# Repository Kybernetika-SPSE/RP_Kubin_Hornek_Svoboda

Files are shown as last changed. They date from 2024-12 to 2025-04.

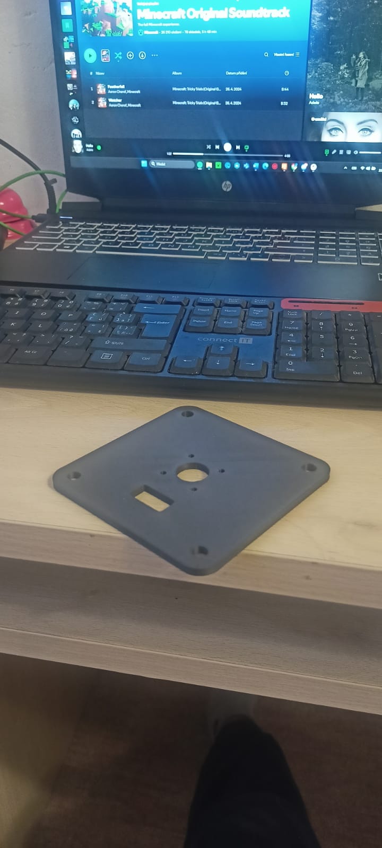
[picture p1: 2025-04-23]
Dokumentace/Progress/Hornek/Dilci_vypracovani/Fotky/m2 podložka.jpg

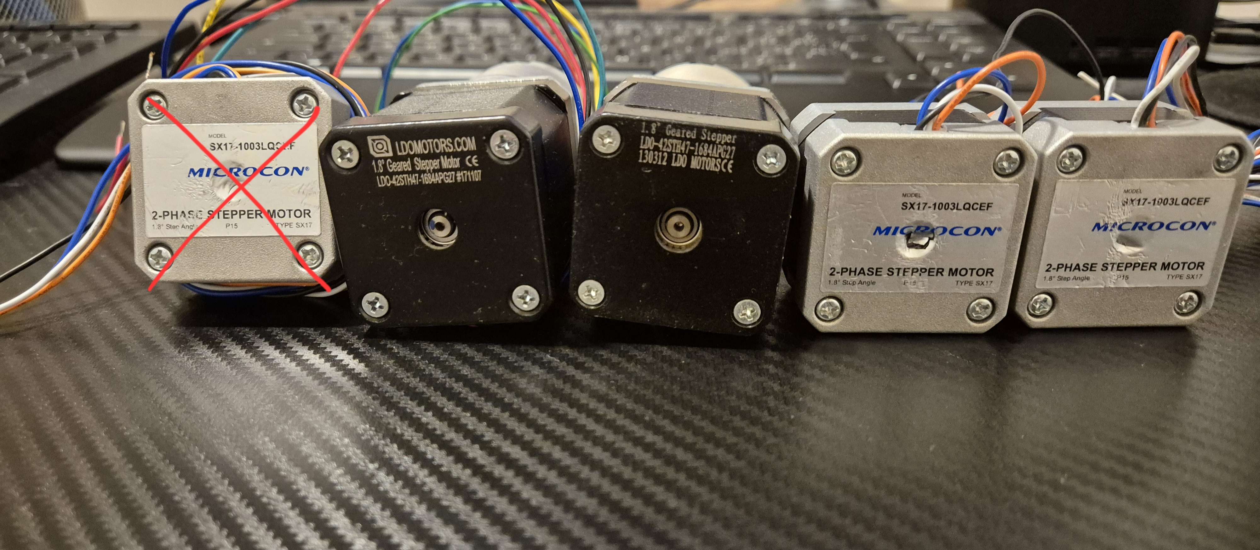
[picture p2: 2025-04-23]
Dokumentace/Progress/Hornek/Dilci_vypracovani/Fotky/20250423_202752.jpg

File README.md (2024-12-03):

Model průmyslového šestiosého robota

Baví nás průmyslové technologie a robotika. Chceme sestavit model průmyslového kolaborativního robota, udělat k němu pendant a provést oživení.
Příští rok bychom toto rádi rozvinuli i do maturitní práce. Očekáváme, že získáme více praxe a více porozumění v tomto oboru a do budoucna nám budou velmi přínosné, ať už v práci, nebo na vysoké škole.
A hlavně... jsme borci

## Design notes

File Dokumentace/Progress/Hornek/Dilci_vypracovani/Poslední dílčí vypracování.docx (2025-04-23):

# Poslední dílčí vypracování

V složce robot jsou veškeré modely, které jsou ve finálním stavu a už se nebudou měnit, takže robot má 4 funkční osy, na dalších dvou se pracuje a brzo budou. Ve složce fotky jsou fotky částí robota, které jsou úspěšně vytisklé. Máme tam dále fotku všech motorů a jednoho motoru na kterém je spojka, kterou budu využívat k uchycení mezi 3. a 4. osou, a mezi 4. a 5. osou. Odkaz na ní: https://www.laskakit.cz/pruzna-spojka-hlinikova-sviraci-5x8mm/

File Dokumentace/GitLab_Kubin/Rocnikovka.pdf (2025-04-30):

## Vyšší odborná škola

## a Střední průmyslová škola elektrotechnická

## Plzeň, Koterovská 85

## ROCNˇ ÍKOVA PR ´ ACE ´

### Téma:

# Model průmyslového šestiosého robota

Autor práce: | Tomáš Kubín
Třída: | 3.L

## Vedoucí práce: Jiří Svihla ˇ

Dne: | 30. 4. 2025

## Hodnocení:

V Plzni dne: 29. 11. 2024 | Mgr. Jan Syřínek, v.r. Zástupce ŘŠ, zástupce statutárního orgánu Vedoucí organizace VOŠ, SŠ, DM

## Vyšší odborná škola a Střední průmyslová škola elektrotechnická Plzeň, Koterovská 85

## Z A D Á N Í R O Č N Í K O V É P R Á C E

Školní rok | 2024/2025
Studijní obor | 78 – 42 – M/01 Technické lyceum
Jméno a příjmení | Tomáš Kubín
Třída | 3.L
Předmět | Kybernetika
Hodnoceno v předmětu | Kybernetika
Téma | Model průmyslového šestiosého robota
Obsah práce | Tvorba řízení (softwarová část) pro model průmyslového kolaborativního robota. • Výběr komponent (20. 12. 2024) • Prototyp řízení (24. 1. 2025) • Finalizace zařízení a napojení na síť (28. 2. 2025) • Tvorba dokumentace (28. 3. 2025)
Zadávající učitel Příjmení, jméno | Švihla Jiří
Termín odevzdání | 30. dubna 2025

## Anotace a poděkování

Má ročníková práce se zabývá tvorbou řízení pro model kolaborativního průmyslového

robota. Cílem bylo vytvořit ne příliš komplexní, avšak efektivní systém jako celek za

pomoci běžně dostupných komponent. Na jiných částech robota pracovali Daniel Hornek

a Matěj Svoboda.

Chtěl bych poděkovat firmě Würth Elektronik za poskytnutí pasivních a elektromechanických součástek do desky plošných spojů zdarma, vedoucímu práce Jiřímu Svihlovi za ˇ

podporu při zpracování, krokové motory a vyfrézování.

Prohlašuji, že jsem tuto práci vypracoval samostatně a použil literárních pramenů a informací,

které cituji a uvádím v seznamu použité literatury a zdrojů informací.

Prohlašuji, že jsem nástroje UI využil v souladu s principy akademické integrity a že na

využití těchto nástrojů v práci vhodným způsobem odkazuji.

Nesouhlasím s využitím mé práce učiteli VOS a SP ˇ | SE Plzeň k výuce. ˇ
V Plzni dne 30. 4. 2025 | Podpis: |

## Obsah

Uvod ´ | 6
1 Cíle | 7
2 Komponenty | 9
3 Návrhový software | 14
4 Komunikace | 18

5 Kód na Raspberry Pi Pico | 21
6 Kód na Raspberry Pi 4 | 24
Závěr | 26
Přílohy | I

## Uvod ´

V současné době, kdy se rozvíjí koncept průmyslu 4.0, je trendem výrobní procesy co

nejvíce automatizovat, a proto se hojně využívá robotů. Kolaborativní roboti jsou schopni

spolupracovat s člověkem za absence většiny bezpečnostních prvků nutných u tzv. dospělých

robotů. To mě dovedlo k myšlence zkusit si jednoho postavit, protože v běžném provozu

si s nimi člověk hrát nemůže a nejedná se ani o běžně přístupné ”hračky.”

Podílení na stavbě jednoho je přínosnou zkušeností nejen z kreativního a programátorského

hlediska, ale i z oblasti spolupráce a organizace projektu více lidí.

6

## 1 Cíle

Mým cílem bylo vyvinout řízení pro model průmyslového robota. Věnoval jsem jak soft-

warové části řízení, tak i té nezbytné hardwarové.

### 1.1 Softwarové cíle

Software jsem nechtěl od samého začátku dělat zbytečně komplikovaný, funkčnosti a od-

laděnosti jsem dával přednost. Programoval jsem s myšlenkou variabilnějšího použití ro-

bota, mezi které řadím například modularitu, jiné počty a typy motorů. Tedy jsem neo-

pomenul rozšíření projektu v budoucnu do takové míry, kdy bude v podstatě jen stačit

změnit konfigurační soubor.

Cíle bych shrnul následovně:

1. Základní ovládání motorů
2. Komunikace
3. Optimalizace a přidání ”nice to have”funkcí

### 1.2 Hardwarové cíle

Již od začátku jsem chtěl všechno umístit do rozvaděče. Tomu jsem uzpůsobil výběr komponent. To bylo primárním důvodem pro návrh vlastní desky plošných spojů (DPS). Mi-

nimalizace byla pro mě nesmírně důležitá, chtěl jsem alespoň vnější konstrukci rozvaděče

být schopen vytisknout na klasické 3D tiskárně.

Shrnutí cílů:

7

1. Výběr komponent
2. Návrh DPS
3. Tvorba rozvaděče

8

## 2 Komponenty

### 2.1 Raspberry Pi Pico 2

Aby bylo zajištěno rychlé ovládání motorů, byl zvolen mikrokontrolér Raspberry Pi Pico 2.

Ten slouží výhradně k obsluze vstupů a výstupů. Přistoupil jsem k variantě bez bezdrátových

možností, všechna komunikace je totiž řešena spolehlivě drátovou cestou.

Raspberry Pico 2 je vybaveno procesorem RP2350A vlastní výroby - dvě jádra M33 Cortex a frekvence 150 MHz. Na desce je 4 MB flash pamět’, která postačí i na náročnější

projekty. Pamět’ RAM je v porovnání s předchozí generací téměř dvojnásobná, tzn. 520

KB. (Raspberry Pi Ltd 2025b)

Velkou výhodou této desky je její popularita ve světě. To se odráží na její dostupnosti a v komunitě není obtížné najít pomoc při případných obtížích (hardwarových i softwa-

rových).

Já osobně ji programuji v MicroPythonu, lze však využít i jazyk C a Arduino IDE.

Celkem má 40 pinů, dvacet na každé straně. Rozmístění pinů včetně popisků mnou

použitých je na výňatku z přílohy I, na obrázku 2.1. Všech 28 dostupných GPIO pinů je

využito.

UART má dva kanály, z nichž jsem použil ten druhý a má pevně dané piny 6 a 7 na levé

straně.

Napájení je zajištěno přes VSYS. Mezi zdrojem a VSYS je ještě zapojena schottkyho

dioda, aby nedocházelo ke zpětnému napájení.

9

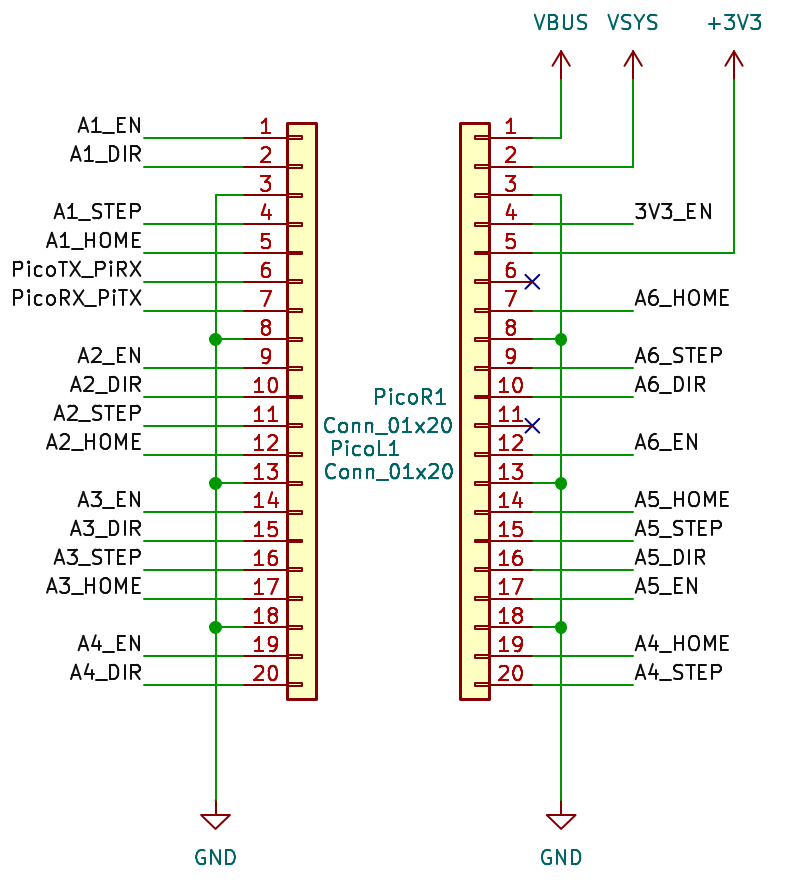
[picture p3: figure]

Obrázek 2.1: Zapojení pinů na Picu [Zdroj: vlastní]

10

### 2.2 Raspberry Pi 4

Raspberry Pi 4 není mikrokontrolérem, nýbrž se jedná o relativně výkonný a univerzální jednodeskový počítač. V mém projektu zajišt’uje komunikaci s mikrokontrolérem a pen-

dantem.

Mezi jeho hlavní přednosti se v mém případě řadí možnost instalace plnohodnotného

operačního systému, což je ideální pro budoucí rozšíření, jako je například hostování

vlastní databáze, webového serveru či jiných náročnějších aplikací.

Stejně jako Raspberry Pi Pico je široce rozšířené a dostává se podpory rozsáhlé komunity.

Má taktéž 40 pinů, v nichž se od Raspberry Pi Pico velmi liší. Za mě je významnou

výhodou více kanálů pro UART. Lze tedy k němu připojit moje Pico, pendant a ještě zůstane velká rezerva. (Raspberry Pi Ltd 2025a)

### 2.3 Drivery pro krokové motory DRV 8825

Pro řízení krokových motorů je nutné použití driveru. Po konzultaci jsem se rozhodl pro DRV8825 od Texas Instruments. Je určen pro bipolární krokové motory (motor má dvě

cívky, tedy z něj vedou 4 dráty, které musíme zapojit) použité v projektu.

Nastavení proudového limitu je možné pomocí malého potenciometru, což chrání motor.

Vyšší proudy vyžadují chlazení, alespoň pasivní.

Neméně důležitou vlastností je mikrokrokování (úprava počtu kroků na celou otáčku), to

lze nastavit v rozsahu od 1 až po 1/32 (zmenšit jde jen po polovinách).

Rozmístění pinů je na obrázku 2.3 (Bakker 2025).

Piny M0, M1, M2 slouží k nastavení mikrokrokování, návod je na DPS.

K pinům A1, A2, B1 a B2 se připojuje vinutí motoru.

Pro funkci je nutné přivést 3 V na piny RESET a SLEEP.

11

Pin ENABLE je vždy zapojen na výstup, aby se motory daly jednoduše vypnout.

Na VMOT je přivedeno 12 V jako napájení motorů. Driver umí i motory s větším vstupním

napětím.

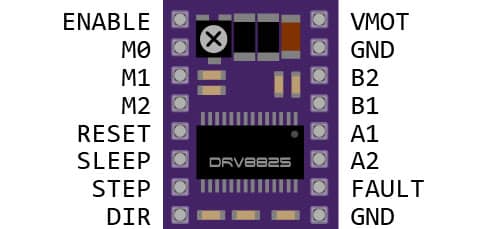
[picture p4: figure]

Obrázek 2.2: Rozmíst’ěný pinů na driveru [Zdroj: makerguides.com]

### 2.4 Rozvaděč

Rozvaděč jsem vymyslel do jisté míry modulární. Spodní a horní část jsem navrhl tak,

aby se dala bez problému vytisknout na 3D tiskárně. Obě části mají výřezy na zasouvací

stěny.

Hrany stěn a složité útvary, které by nešly vytvořit jiným způsobem, jsou vyfrézovány do dřevěné desky o tloušt’ce 3 mm. Díry pro úchyty DPS, Raspberry Pi 4, zdroje jsou

dodatečně vyvrtány vrtačkou a tudíž nebudou zahrnuty ve výkresech. Zdrojové soubory pro rozvaděč jsou v GitHub repozitáři (Kubín 2025).

12

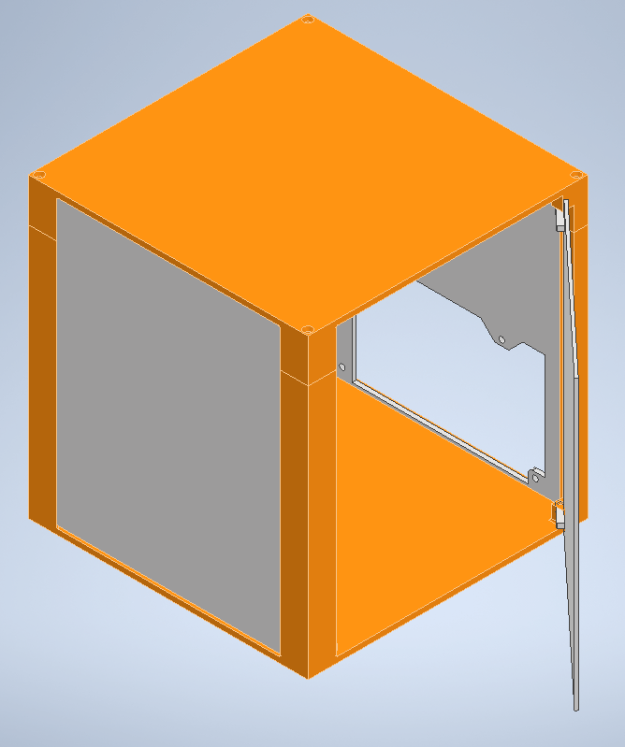
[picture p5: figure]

Obrázek 2.3: Rozvaděč ve 3D návrhovém softwaru [Zdroj: vlastní]

13

## 3 Návrhový software

Po výběru komponent bylo důležité se rozhodnout, v jakých jazycích a nástrojích budu

tvořit.

### 3.1 Visual Studio Code (VS Code)

Veškerý kód jsem vyvíjel v jazyce Python (resp. MicroPython). Rozhodl jsem se pro

populární IDE Visual Studio Code vyvíjené společností Microsoft. Zkoušel jsem předtím

často v komunitě doporučovaný Thonny, ale ten mi připadal jako příliš jednoduchý a omezující

program.

Mezi nejdůležitější přednosti VS Code řadím hlavně ty zvyšující uživatelský komfort. VS

Code má pro mě nesmírně důležité zkratky ”Ctrl+Tab”a skvěle fungující ”Tab”, které

bohužel stále v dnešní době moc programů neumí. Nabízí možnost členit kód do regionů,

které lze skrýt, což je výrazná výhoda pro lepší orientaci.

Na obrázku 3.1 je prostředí s otevřeným kódem. Na obrázku 3.2 je detail pravého horního

rohu, kde se v přehledu ukazují názvy regionů, případně se zvýrazní stejné proměnné, když

na nějaké stojíte.

Do VS Code jde doinstalovat spoustu rozšíření, kterých jsem samozřejmě využíval.

Primárně tyto:

1. Micro Pico (Random Nerd Tutorials 2025)

Tento doplněk umožňuje programovat Raspberry Pi Pico. Umožňuje i ukládání

a mazání souborů z Pica. Slouží také ke spouštění kódů na Picu bez nutnosti je

mít na něm uložené a čtení dat z konzole.

2. Remote Explorer

14

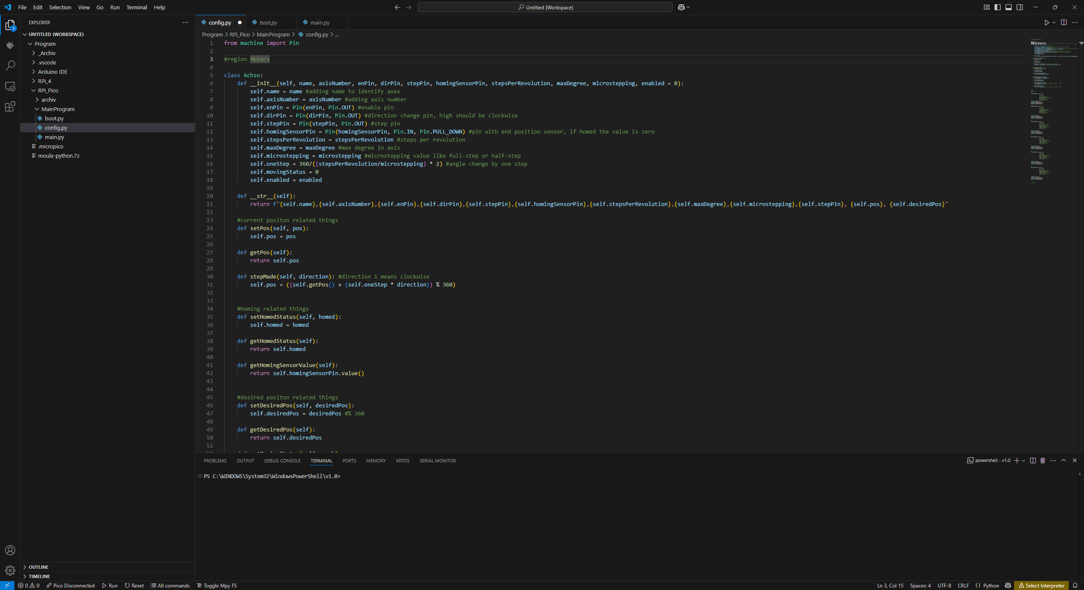
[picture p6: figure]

Obrázek 3.1: VS Code s otevřeným python skriptem [Zdroj: vlastní]

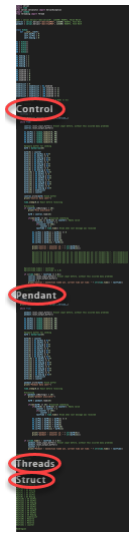
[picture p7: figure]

Obrázek 3.2: Detail pravého horního rohu z VS Code [Zdroj: vlastní]

15

Jedná se o doplněk, který se prostřednictvím SSH připojí na vzdálenou stanici,

my mu specifikujeme, kterou složku má vždy otevřít, tou procházíme a otevíráme

soubory s kódem, které po každé změně musíme uložit a přes terminál ve spodní

části obrazovky spustit.

### 3.2 KiCad

KiCad je volně dostupným programem pro návrh desek plošných spojů (DPS). Já jakožto

začátečník oceňuji jeho jednoduchost a hned jsem se s ním sžil.

Jedná se v podstatě o balík různých nástrojů, do kterých je i členěn viz. obrázek 3.4,

a ty pospolu fungují jako celek. Mezi mnou nejvíce využívané patří schematický, PCB

a footprint editor.

KiCad umožňuje instalaci doplňků, které mohou zjednodušit export potřebných souborů pro výrobu specializovanou firmou. Můj projekt je na GitHubu (Kubín 2025).

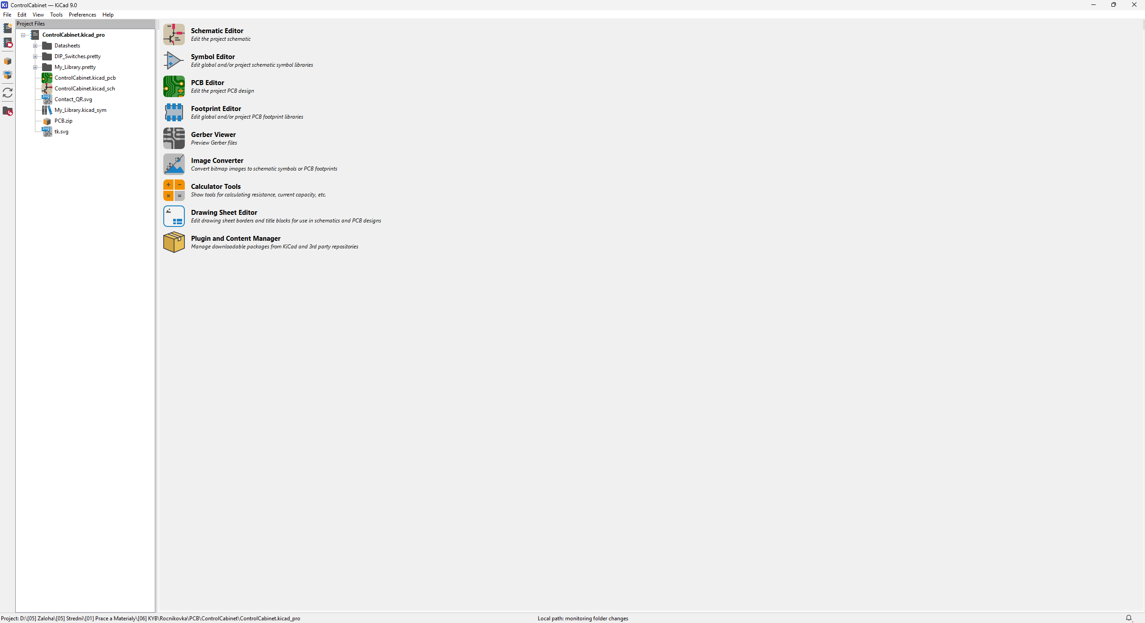
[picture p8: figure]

Obrázek 3.3: Pohled na základní prostředí KiCadu s otevřeným projektem [Zdroj: vlastní]

16

### 3.3 Autodesk Inventor

3D modely pro rozvaděč jsem vytvářel v profesionálním programu Autodesk Inventor.

Jedná se o program, který využívá naše škola ve výuce. Proto mi nepřišel cizí a odpadlo

učení se něčeho nového.

Kromě tvorby 3D modelů umožňuje i vytváření sestav a výkresů. Výkresy se nechají

všelijak upravovat, vlastní razítko, rámečky atd.

Nativně podporuje export modelů do .stl či .stp souborů pro tisk.

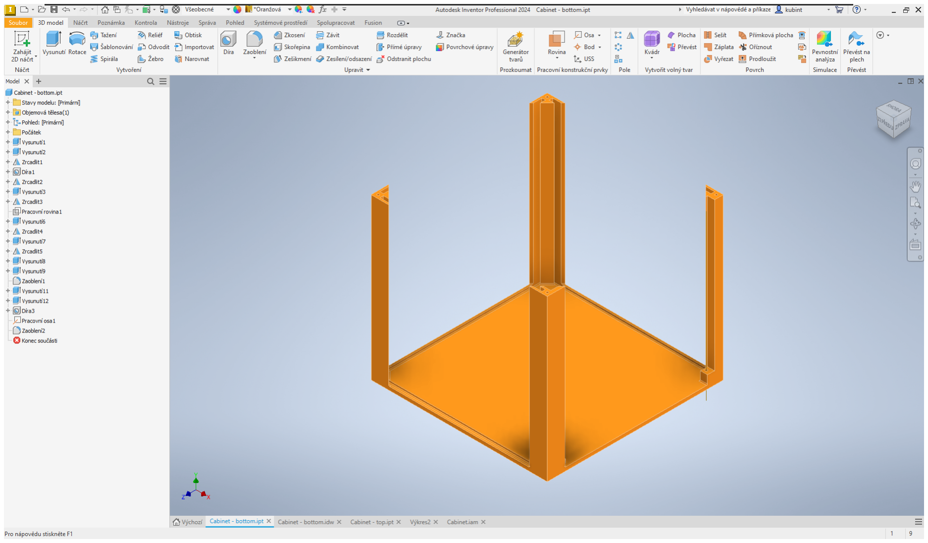
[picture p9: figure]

Obrázek 3.4: Pohled na základní prostředí Inventoru s otevřeným projektem [Zdroj: vlastní]

17

## 4 Komunikace

Komunikace mezi oběma Raspberry a pendantem je dělána přes UART. Jedná se o jedno-

duchý asynchronní komunikační protokol, kterému stačí jen dva vodiče. Po jednom jedna strana odesílá data (Tx) a druhá přijímá (Rx), u druhého drátu je směr komunikace

opačný.

UART dovoluje nastavit přenosovou rychlost (baudrate), jinými slovy počet bitů za

sekundu (bps). Já osobně jsem se rozhodl pro 115 200 bps, jedná se o kompromis mezi

rychlostí a spolehlivostí (ani na jedno si nemohu stěžovat)

V pythonu je jeho použití v kódu velmi jednoduché, netřeba instalovat dodatečné knihovny.

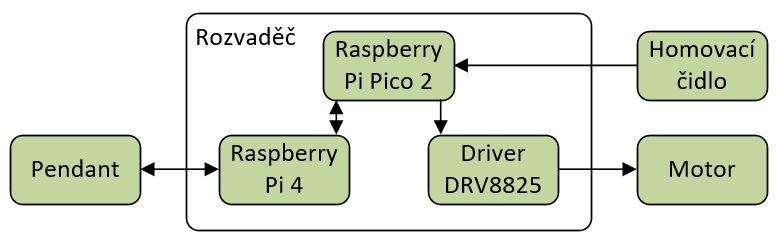
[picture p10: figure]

Obrázek 4.1: Komunikační diagram [Zdroj: vlastní]

### 4.1 Struktura dat

V rámci přehlednosti a rozumné kontroly nad posílanými daty jsem se rozhodl posílat

si vždy stejně dlouhé pole bajtů. Jeho struktura je popsána v tabulce 4.1. Struktura je

všude stejná jak pro Raspberry Pi Pico 2 tak pro pendant, jen některé hodnoty mají jiný význam (jednou aktuální pozice a jindy zas požadovaná).

Rozhodl jsem se pro 24 bajtů, nejedná se sice pěkně o mocninu dvou, ale nechtěl jsem

dělat zbytečně velkou rezervu. Rezervu jsem přidal pro jednoduchost přidávání budoucích

dat, odpadá potom nějaké to psaní navíc na všech stranách, takhle stačí jen menší úprava.

18

Pořadí bytu | Jeho obsah
0 | counter
1 | 1. byte požadované pozice první osy
2 | 2. byte požadované pozice první osy
3 | homing k první ose
4 | 1. byte požadované pozice druhé osy
5 | 2. byte požadované pozice druhé osy
6 | homing k druhé ose
7 | 1. byte požadované pozice třetí osy
8 | 2. byte požadované pozice třetí osy
9 | homing k třetí ose
10 | 1. byte požadované pozice čtvrté osy
11 | 2. byte požadované pozice čtvrté osy
12 | homing k čtvrté ose
13 | 1. byte požadované pozice páté osy
14 | 2. byte požadované pozice páté osy
15 | homing k páté ose
16 | 1. byte požadované pozice šesté osy osy
17 | 2. byte požadované pozice šesté osy
18 | homing k šesté ose
19 | seznam povolených os
20-22 | rezerva
23 | counter

Tabulka 4.1: Struktura posílaných dat z Raspberry Pi 4

19

První a poslední bajt obsahují vždy stejný counter (proměnná, která se čítá s každým

odesláním), který slouží k detekci přijatých nových dat a zároveň kontrole konzistence

(všechna data přišla v pořádku).

Natočení osy může být od 0° do 360°, zatímco maximální hodnota jednoho bajtu může

být 255. Proto jsem musel úhel natočení pomocí bitových operací rozdělit do dvou bajtů.

Následuje bajt, ve kterém jsou věci k homingu. Zatím se jedná spíše o neefektivně využitý

bajt, protože se v něm posílá jen jestli je osa homovaná respektive jestli má povolení se

homovat. V plánu je ale budoucí rozšíření, kde počítám s více parametry, proto tam tedy

nechávám jednotlivé bajty.

V 19. bajtu každý bit až na poslední je přiřazen jedné ose. Hodnota bitu TRUE znamená,

že osa je povolena, zatímco FALSE znamená, že je zakázána.

V budoucnu je v plánu strukturu upravit na posílání i desetinných čísel v případě natočení

motorů.

20

## 5 Kód na Raspberry Pi Pico

Veškerý kód tvořený pro Raspberry Pi Pico 2 jsem na něj uložil ve třech souborech. A je dostupný na GitHub repozitáři (Kubín 2025)

### 5.1 boot.py

Vlastností firmwaru je, že se soubor boot.py, je-li k dispozici, spustí automaticky po připojení napájení. Já osobně v něm jenom zablikám s LED, at’ vím, že Pico právě naběhlo.

### 5.2 main.py

Po dokončení kódu z boot.py se automaticky spustí main.py. V mém případě se jedná tedy

o soubor, ve kterém je uložen hlavní kód.

### 5.2.1 Vlákna

Z důvodu rychlosti (stačil jen jeden motor a byl poznat rozdíl) jsem musel implementovat

multithreading. Vytvořil jsem dvě vlákna, to první se stará o komunikaci s Raspberry Pi

4 přes UART a to druhé řeší pohyb motorů. Vlákna spolu sdílejí proměnné.

Napřed je třeba import knihovny _thread. V kódu mám vytvořené ony dvě funkce

s cyklem while. Vlákna se startují velmi jednoduše ve dvou řádcích:

second_thread = _thread.start_new_thread(control_thread, ())

uart_thread()

21

### 5.3 config.py

Soubor config.py je tvořen v podstatě jako knihovna. Je importován na začátku souboru

main.py.

Je v něm napsána poměrně rozsáhlá třída, která obsahuje veškeré vlastnosti pro jednotlivé

motory na každé ose.

Třída se v Pythonu vytváří následovně:

class Achse:

To ale samo o sobě nestačí, dovnitř začneme psát různé funkce. Asi tou nejdůležitější je

__init__, její vstupními parametry jsou v mém případě:

self, name, axisNumber, enPin, dirPin, stepPin, homingSensorPin, stepsPerRe-

volution, maxDegree, microstepping, enabled = 0.

Self je povinný argument. Vstupní proměnné obsahující slovo Pin jsou přímo číslo pinu,

na který je daná věc zapojena. Ostatní vstupní hodnoty jsou vlastnosti specifické pro

každou osu.

Dále obsahuje 11 funkcí, které zahrnují mimo jiné i nastavení požadované pozice, čtení

aktuální pozice a veškeré věci týkající se homování.

Po deklaraci třídy je potřeba vytvořit si proměnné (pro každou osu jednu). Pro lepší práci

s osami jsem si napřed vytvořil pole, do kterého jsem vložil proměnnou od každé osy. Na

obrázku 5.2 je vidět deklarace pole a připojení první osy k němu.

22

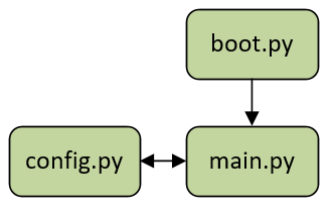
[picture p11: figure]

Obrázek 5.1: Diagram spouštění kódu na Pico 2 [Zdroj: vlastní]

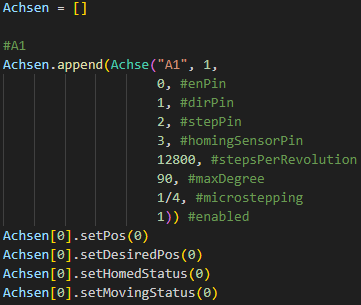
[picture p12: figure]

Obrázek 5.2: Připojení proměnné pro první osu do pole [Zdroj: vlastní]

23

## 6 Kód na Raspberry Pi 4

Situace se soubory je tentokrát mnohem jednodušší. Vše je psáno v souboru main.py.

Na rozdíl od Raspberry Pi Pico jsem musel ještě v pár jednoduchých krocích nastavit spouštění skriptu po startu. Kód je též na GitHubu (Kubín 2025).

### 6.1 Autostart skriptu

Postup pro nastavení automatického spouštění skriptu:

1. Spustíme terminál (lze i vzdáleně pomocí ssh, já preferuji program KiTTY)
2. Spustíme program crontab s parametrem e

crontab -e

3. Jsme dotázáni, v jakém editoru chceme editovat, volba je čistě na Vás
4. Pro spuštění kódu hned po startu přidáme do souboru

@reboot python3 /home/Code/main.py

5. Soubor uložíme a můžeme restartovat pro ověření funkčnosti. (Brown 2025)

### 6.2 Vlákna

Kód je i zde rozdělen do dvou vláken, jen pomocí knihovny threading. Implementace je

potom též poměrně jednoduchá a ve dvou řádcích:

Thread(target = comm_Control).start()

Thread(target = comm_Pendant).start()

24

Vlákna sdílejí některé proměnné. Jedná se jen o proměnné třídy s osami.

Spuštěné funkce si jsou velmi podobné, liší se jen drobnostmi. Já tedy vysvětlím jen

princip funkčnosti. Zakládal jsem si na tom, že zařízení jako celek bude ve stylu plug

and play, člověk se nebude muset o nic starat a po zapnutí napájení se komunikace sama

naváže.

Jsou použity dvě hlavní proměnné pro správu counter a lastTime, kdy nutnost counteru

již byla vysvětlena a proměnná lastTime, ukládající čas poslední komunikace, je nezbytně nutná pro detekci výpadku spojení (timeout).

Po naplnění send bufferu se buffer odešle. Raspberry chvíli čeká na odpověd’. Když přijdou

nějaká data, zkontroluje jejich validitu. Jestli jsou data validní, zpracuje je a inkrememn-

tuje counter pro další interakci.

Když data validní nejsou, tak posílá a stále na ně čeká. Pokud již dlouho k žádné komu-

nikaci nedošlo, counter se vyresetuje a Raspberry se spojení snaží navázat znovu.

25

## Závěr

Cílem mé práce bylo udělat řízení pro model průmyslového šestiosého kolaborativního

robota.

Komponenty byly vybrány vhodně a integrovány. Na mou první takovou zkušenost si myslím, že množství chyb (ne perfektně povedených věcí) je až příliš nízké. Ale i tak jsem

určitě pro příště poučen a vím, co dělat jinak nebo lépe.

Vytvořený projekt lze použít jako základ pro budoucí rozšíření jak robota, tak i softwarové

stránky.

Práce mě seznámila s novými věcmi, získal jsem zkušenosti z oblasti softwaru a návrhu

vlastní desky plošných spojů.

26

## Seznam obrázků

2.1 Zapojení pinů na Picu [Zdroj: vlastní] | 10
2.2 Rozmíst’ěný pinů na driveru [Zdroj: makerguides.com] | 12
2.3 Rozvaděč ve 3D návrhovém softwaru [Zdroj: vlastní] | 13
3.1 VS Code s otevřeným python skriptem [Zdroj: vlastní] | 15
3.2 Detail pravého horního rohu z VS Code [Zdroj: vlastní] | 15

3.3 Pohled na základní prostředí KiCadu s otevřeným projektem [Zdroj: vlastní] 16

3.4 Pohled na základní prostředí Inventoru s otevřeným projektem [Zdroj: vlastní] 17

4.1 Komunikační diagram [Zdroj: vlastní] | 18
5.1 Diagram spouštění kódu na Pico 2 [Zdroj: vlastní] | 23
5.2 Připojení proměnné pro první osu do pole [Zdroj: vlastní] | 23

27

## Bibliografie

Bakker, Benne de (2025). “How to control a stepper motor with DRV8825 driver and Ar-

duino”. In: Maker Guides. doi: https://www.makerguides.com/drv8825-stepper-

motor-driver-arduino-tutorial/. (https://doi.org/https://www.makerguides.com/drv8825-stepper-motor-driver-arduino-tutorial/)
Brown, Korbin (2025). “Automating Raspberry Pi: How to Autostart Programs”. In:

Linux Config. doi: https://linuxconfig.org/automating- raspberry- pi- how-

to-autostart-programs. (https://doi.org/https://linuxconfig.org/automating-raspberry-pi-how-to-autostart-programs)
Kubín, Tomáš (2025). RPKubinHornekSvoboda/Code/Rizeni/. url: https://github.

com/Kybernetika-SPSE/RP_Kubin_Hornek_Svoboda/tree/main (https://github.com/Kybernetika-SPSE/RP_Kubin_Hornek_Svoboda/tree/main) (cit. 27. 04. 2025).

Random Nerd Tutorials (2025). “Programming Raspberry Pi Pico with VS Code and

MicroPython”. In: Random Nerd Tutorials. doi: https://randomnerdtutorials.

com/raspberry-pi-pico-vs-code-micropython/. (https://doi.org/https://randomnerdtutorials.com/raspberry-pi-pico-vs-code-micropython/)
Raspberry Pi Ltd (2025a). Raspberry Pi Hardware. url: https://www.raspberrypi.

com/documentation/computers/raspberry-pi.html (https://www.raspberrypi.com/documentation/computers/raspberry-pi.html) (cit. 27. 04. 2025).

— (2025b). RP2350 Datasheet. url: https://datasheets.raspberrypi.com/rp2350/

rp2350-datasheet.pdf (https://datasheets.raspberrypi.com/rp2350/rp2350-datasheet.pdf) (cit. 27. 04. 2025).

28

## Přílohy

Příloha I: Schéma zapojení

Příloha II: Schéma DPS

Příloha III: Spodek rozvaděče

Příloha IV: Vršek rozvaděče

Příloha V: Levá + zadní stěna rozvaděče

Příloha VI: Pravá stěna rozvaděče

Příloha VII: Rozvaděč

I

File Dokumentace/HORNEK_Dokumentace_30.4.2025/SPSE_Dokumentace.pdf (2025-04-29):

[R]1

## Vyšší odborná škola

## a Střední průmyslová škola elektrotechnická

## Plzeň, Koterovská 85

## ROCNˇ ÍKOVA PR ´ ACE ´

### Téma:

# Model průmyslového šestiosého robota

Autor práce: | Daniel Hornek
Třída: | 3.L

## Vedoucí práce: Jíří Svihla ˇ

Dne: | 30.5.2025

## Hodnocení:

ZDE VLOZIT LIST ZAD ˇ | AN´ Í

Z důvodu správného číslování stránek

## Anotace a poděkování

Model šestiosého kolaborativního půrmyslového robota, který reaguje na prostředí. Zabýval

jsem se modelováním a sestavením šestiosého robota. Cílem byl funkční šestiosé robotické

rameno. Na práci jsem pracoval společně s spolužákem Tomášem Kubínem, který vytvářel

software a rozvaděč a s spolužákem Matějem Svobodou, který pracoval na pendandu (uživatelské rozhraní).

Chtěl bych poděkovat vedoucímu práce Jiřímu Svihlovy za podporu při zpracování a ˇ

za poskytnutí krokových motorů. Dále bych chtěl poděkovat svému spolužákovy Vítu

Moulisovi, který mi zpřístupněl jeho 3D tiskárnu.

Prohlašuji, že jsem tuto práci vypracoval samostatně a použil literárních pramenů a informací,

které cituji a uvádím v seznamu použité literatury a zdrojů informací.

Prohlašuji, že jsem nástroje UI využil v souladu s principy akademické integrity a že na

využití těchto nástrojů v práci vhodným způsobem odkazuji.

Souhlasím s využitím mé práce učiteli VOS a SP ˇ | SE Plzeň k výuce. ˇ
V Plzni dne 30.5.2025 | Podpis: |

## Obsah

Uvod ´ | 6
1 Cíl | 7
2 Součástky | 8
3 Softwarové aplikace | 11
4 Modely | 14

4

Závěr | 24
Přílohy | I

## Uvod ´

V součastnosti se stávají roboti nedílnou součástí života. V průmyslu se začínají kola-

borativní roboti využívat čím dál tím častěji. A tak mě zajímalo jak těžké je takového

robota postavit. A tak jsem se dal do modelování robota.

6

## 1 Cíl

Můj cíl byl nadesignovat, vymodelovat a postavit robota. Věnoval jsem výhradně hard-

waru robota.

### 1.1 Design

Jedním z cílu bylo vytvořit robota tak, aby se na něj dalo koukat jako na něco úžasného.

Chtěl jsem taky aby robot byl co nejmenší.

### 1.2 Model

Hlavní cíl byla ale funkčnost robota. Bylo za potřebý vymyslet části tak, aby do sebe

nejen seděli, ale aby taky plnili to co mají.

7

## 2 Součástky

### 2.1 Motory

Pro pohyb robota jsem využil tři typy motorů NEMA 17.

### 2.1.1 LDO-42STH47-1684a

Krokový motor LDO-42STH47-1684A je hybridní motor velikosti NEMA-17. Má vysoký točivý momenta a přesnost. Má krokový úhel 1,8°. Krokový úhel 1,8° znamená, že se o tento

úhel otočí při každém kroku. Motor pracuje na jmenovitém napětí 2,8 V a jmenovitém proudu 1,68 A (LDO MOTORS CO. 2012).

Tento motor je dvoufázový a má indukčnost 2,8 mH na fázi. Jeho hmotnost je 0,35 kg.

Je nejvhodnější na přesné polohování, nejčastěji se užívá u 3D tiskáren.

Tento typ motor je použit 3x v práci a to u prvních třech os. Je to kvůli tomu, že jsou

nejtěžší a že udrží tu největší váhu.

### 2.1.2 SX17-1005LQCEFds

Krokový motor SX17-1005LQCEFds je hybridní dvoufázový motor s přírubou NEMA 17. Má stejný otáčivý moment jako LDO-42STH47-1684a s tolerancí 0,1°. Maximální proud

motoru je 1A a má jmenovité napětí 5,9 V. Jeho přídržný moment je 0,5 Nm (UMAX

2025).

Tento motor se díky své vysoké přesnosti a kompaktonsti využívá u 3D tiskáren.

8

Tento motor jsem v robotovy využil 1x a to u 4. osy, protože se na to hodil rozměrově.

### 2.1.3 SX17-1003LQCEF

Krokový motor SX17-1003LQCEF je hybridní dvoufázový motor s přírubou NEMA 17.

S motorem SX17-1005LQCEFds je jiný pouze ve velikosti a v jeho přídržným momentu, oproti SX17-1005LQCEFds jeho přídržný moment je 0,3 nM (Conquest entertainment

2025).

Tento motor jsem v práci využil 2x a to u 5. a 6. osy, jelikož jsou nejlehčí z uvedených

motorů.

### 2.2 OMRON Koncový spínač pákový 5A 125VAC

OMRON Koncový spínač pákový 5A 125VAC je mikrospínač s konfigurací kontaktů SPDT(Single Pole Double Throw), což znamená, že může přepínat mezi dvěma obvody.

Jeho zatížitelnost kontaktů je 5A při 125 V AC, a to ho činí vyhodným pro průmyslové

aplikace, např. v 3D tiskárnách nebo CNC strojích.

Spínač má jednu stabilní polohu a způsob přepínaní ON-(ON). Jeho mechanická životnost

dosahuje až 30 miliónů cyklů. Elektrická životnost je 200 000 cyklů. Má kompaktní rozměry (19,8 x 6,4 x 10,2 mm), takže je vhodný pro vnitřní použití (OMORON 2025).

Tento spínač využívám jako koncový spínač na určení počáteční polohy. V práci je použit

5x, u každé osy jednou kromě 6. osy.

### 2.3 Pružná spojka hliníková svírací 5x8mm

Je mechanická součástka, která se používá k propojení dvou hřídelí, např. mezi krokovým motorem a závitovou tyčí 3D tiskárny (Botland 2025).

9

Já tuto spojku využil na spojení hřídele motoru s další částí robota. Celkově je v práci

využita 2x.

10

## 3 Softwarové aplikace

Na vymodelování robota jsem využil aplikaci Autodesk Fusion 360. K vytvoření výkresů

k modelům jsem využil aplikaci Autodesk Inventro 2026.

### 3.1 Autodesk Fusion 360

Autodesk Fusion 360 je moderní cloudově založený nástroj, který integruje CAD, CAM

i CAE do jednoho komplexního prostředí. Umožňuje vytváření parametrických i volně

tvarovaných 3D modelů, přičemž výkonné nástroje pro simulace a analýzu ověřují návrhy

dříve, než se dostanou k výrobě. Díky intuitivnímu rozhraní a flexibilitě se snadno osvojuje

jak u profesionálů, tak i u nadšenců.

Další významnou výhodou Fusion 360 je jeho cloudová technologie, která výrazně usnadňuje

spolupráci v týmu. Sdílení projektů v reálném čase, přístup odkudkoliv a pravidelné ak-

tualizace umožňují držet krok s aktuálními trendy v designu i výrobních postupech.

Celkově jde o komplexní řešení pro návrh, simulaci a přípravu výroby, které značně zjed-

nodušuje celý vývojový proces a otevírá dveře k rychlé a efektivní realizaci náročných projektů (Autodesk 2025a) .

Fusion 360 jsem si vybral protože jsem v něm jestě nikdy před tím nepracoval, takže jsem

to byla výzva pro mě, a protože se v něm dělají jednoduše soustavy viz. 3.1. Také mi ho

učitelé doporučili.

### 3.2 Autodesk Inventor 2026

Autodesk Inventor je robustní profesionální nástroj pro 3D mechanické projektování,

který slouží k tvorbě, simulaci i dokumentaci produktů. Nabízí pokročilé možnosti pa-

11

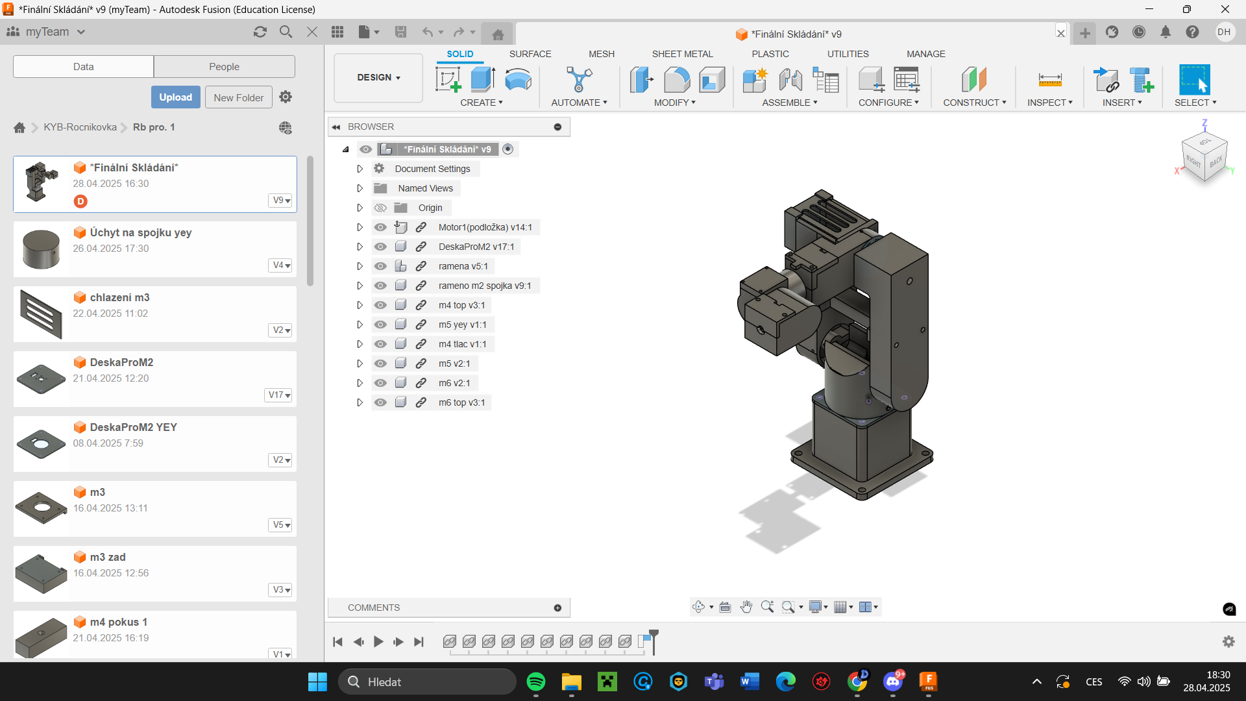
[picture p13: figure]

Obrázek 3.1: Uvodní menu Autodesk Fusion 360 s otevřeným projektem, v tomto případě ´ je to model šestiosého kolaborativního robota

rametrického modelování a přímého modelování, což umožňuje detailní návrh složitých

dílů a sestav v průmyslových i strojírenských aplikacích. Díky integrovaným nástrojům

pro simulaci dynamiky, statiky a tepelných procesů mohou inženýři ověřit design ještě

před samotnou výrobou.

Software se vyznačuje intuitivním rozhraním a širokou škálou funkcí, včetně tvorby po-

drobných výkresových dokumentací a optimalizace výrobních procesů. Integrované nástroje pro správu dat a verzí napomáhají plynulé spolupráci v týmech a zajišt’ují konzistenci de-

signu napříč celým průmyslovým projektem.

Celkově Inventor představuje komplexní řešení pro inženýry a návrháře, které podporuje

inovativní myšlení a umožňuje efektivní přechod od konceptu k finálnímu produktu. Tento

software je oblíbenou volbou v prostředí, kde se vyžaduje vysoká přesnost, efektivita a spolehlivost při tvorbě mechanických zařízení (Autodesk 2025b).

Inventor jsem si vybral protože jsem potřeboval program, ve kterém jdou jednoduše

vytvářet výkresy, a jelikož jsem výkresy již v Inventoru vytvářel, nebyla to pro mě potíž

12

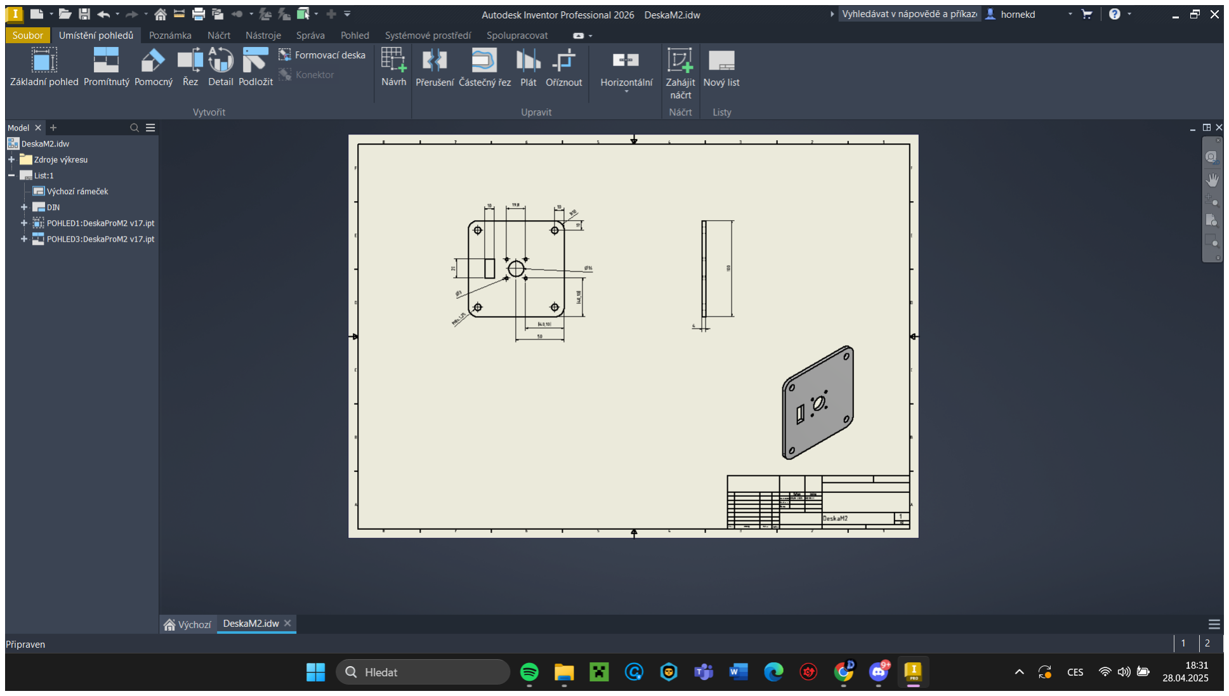
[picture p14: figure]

Obrázek 3.2: Uvodní menu Autodesk Inventro když je odevřený výkres, v tomto případě ´ je otevřený výkres součásti šestiosého kolaborativního robota

viz. 3.2 obrázek . A díky snadnému exportování dokumentů z Autodesk Fusion 360 do

souborů kompatibilní s Inventorem to byla jasná volba.

13

## 4 Modely

V této kapitole vám popíšu každou část modelu robota.

### 4.1 Struktura pro Motor 1

Na obrazku 4.1 mužete vidět strukturu, která slouží jako základna celého robota. V

střední části je místo které slouží na umístění motoru LDO-42STH47-1684a a vedle i na

umístění tlačítka OMORON. Na boku můžeme vidět díru, která slouží jako vývod kabelů.

Pro to aby motor džel na místě slouží ložisko M1 viz. 4.2.

### 4.2 Struktura pro Motor 2

Na obrázku 4.3 mužeme vidět model struktury pro motor 2. Z jedné strany je výseč

pro umístění tlačítka OMORON. Z druhé strany je výstup na kterém bude držet jedno z

ramen viz. 4.4

### 4.3 Struktura pro Motor 3 (Ramena)

Ramena jsou mezi sebou spojeny strukturou na obrázku 4.9. Na ramenu které je na

obrázku 4.5 je v spodní části umístěn úchyt na motor 2 spolu s výstupkem který bude

stlačovat tlačítko pro motor 2. V horní části je struktura na úchyt motoru 3, kdy z jedné

strany bude, na obrázku pro nás nahoře, bude umístěn úchyt na motor s výstupem hřídele

viz. 4.7 a z druhé strany uýhyt 4.8. Na horní část se zasune chlazení které funguje i jako

vývod kabelů viz. 4.6.

14

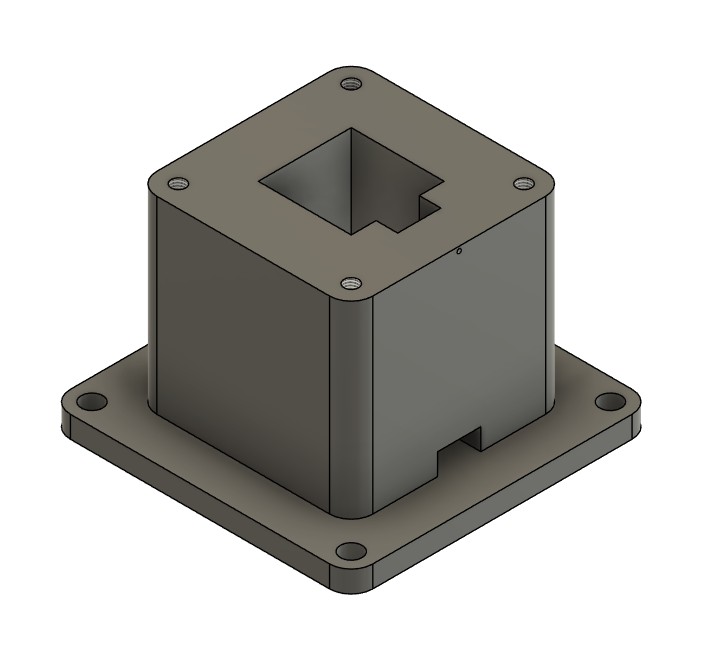
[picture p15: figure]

Obrázek 4.1: Podlozka M1 - Výkres Příloha XI

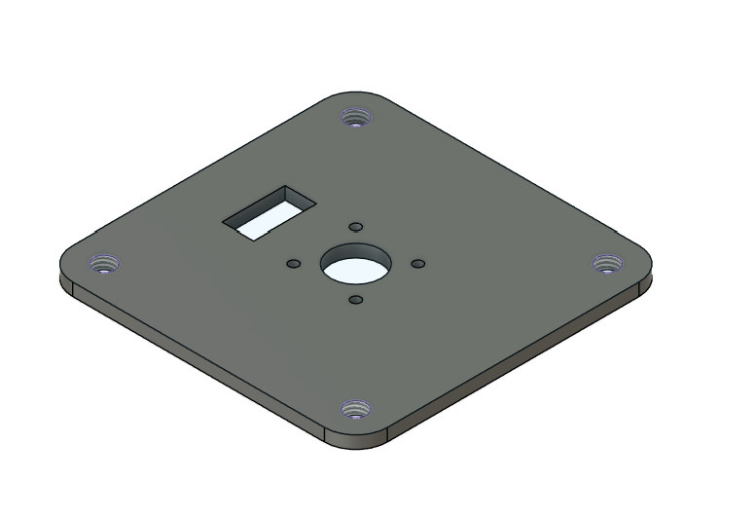
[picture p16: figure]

Obrázek 4.2: Lozisko M1 - Výkres Příloha I

15

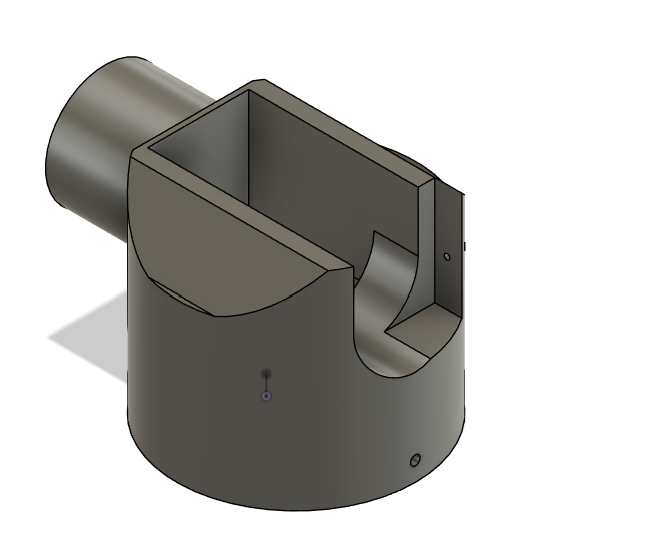
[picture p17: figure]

Obrázek 4.3: PodlozkaM2 s místem pro motor 2 - Výkres Příloha XII

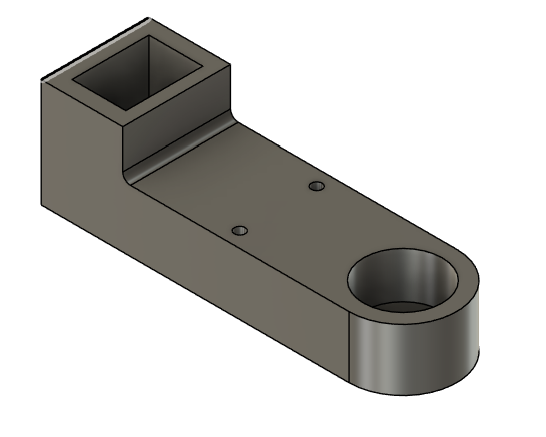
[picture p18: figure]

Obrázek 4.4: Rameno s úchytem na tlacitko - Výkres Příloha XV

16

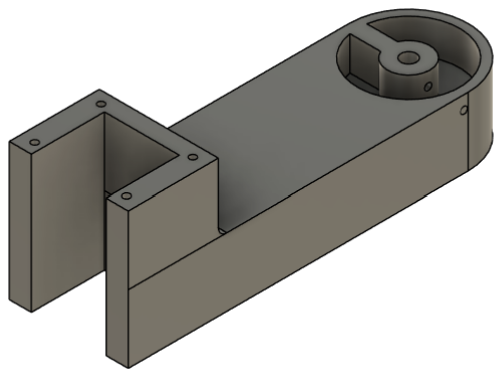
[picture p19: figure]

Obrázek 4.5: Rameno s úchytem na motor 3 - Výkres Příloha XIII

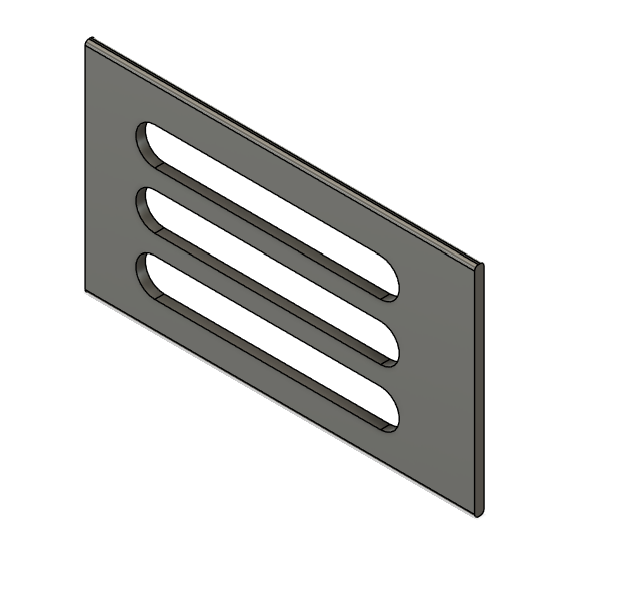
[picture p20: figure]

Obrázek 4.6: Chlazení pro motor 3 - Výkres Příloha IV

17

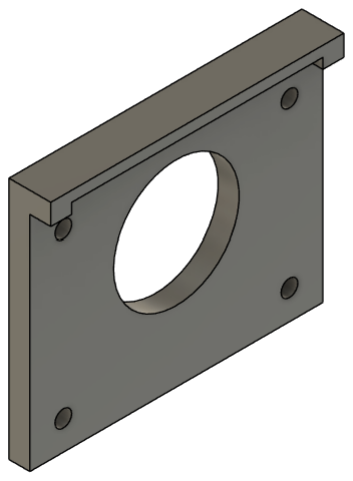
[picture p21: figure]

Obrázek 4.7: Přední část uchycení motoru 3 - Výkres Příloha III

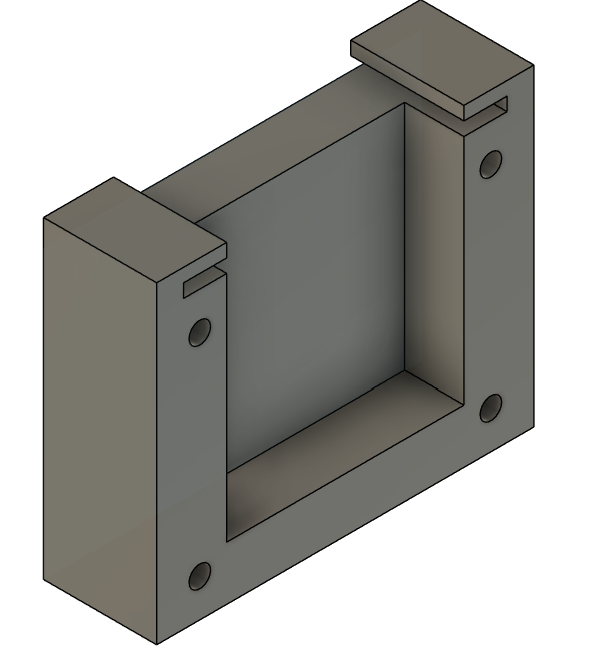
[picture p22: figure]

Obrázek 4.8: Zadní část úchytu pro motor 3 - Výkres Příloha II

18

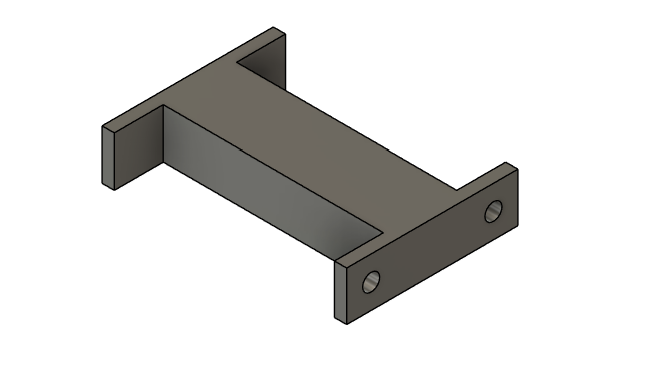
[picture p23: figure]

Obrázek 4.9: Model na způsob jakým budou spojeny ramena - Výkres Příloha XVI

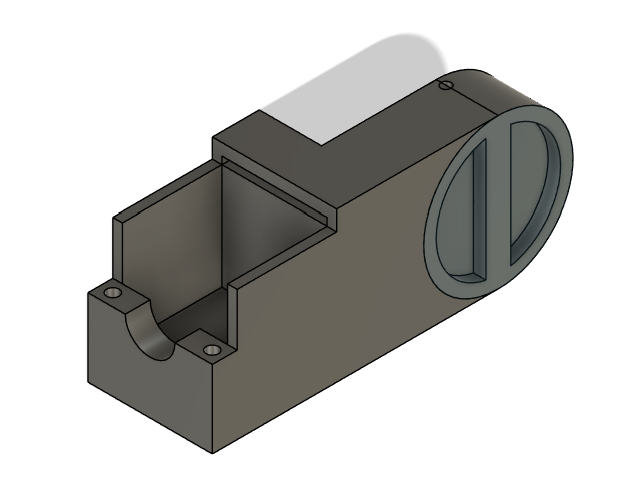
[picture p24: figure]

Obrázek 4.10: Podložka/rameno pro motor 4 - Výkres Příloha XIV

### 4.4 Struktura pro Motor 4

V této části robota kterou můžete vidět na obrázcích 4.10 a 4.11. Na obrázku 4.10

můžeme na zadní části vidět vysuntí, které slouží na stlačení tlačítka OMORON pro

motoru 3 . Přední část robota slouží k uchycení robota, společně se na ní přiloží struktura

na obrázku 4.11 a na ní se příloží 4.12 .

Na struktuře kterou vidíme na obrázku 4.12, můžeme vidět část, která bude stlačovat

tlačítko pro motor 4.

19

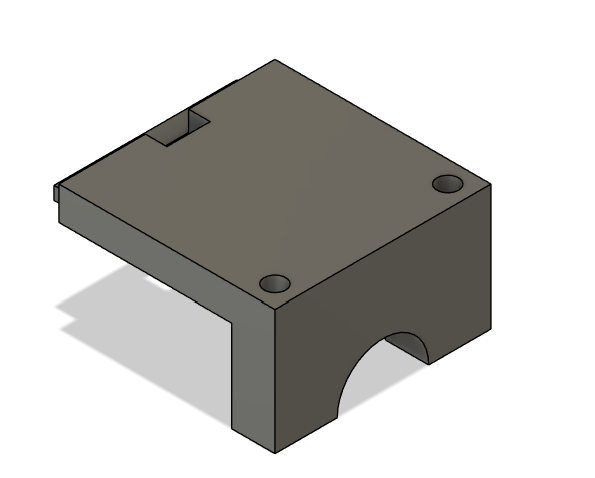
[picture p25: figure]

Obrázek 4.11: Horní část motoru 4 s výstupem pro kabely - Výkres Příloha VI

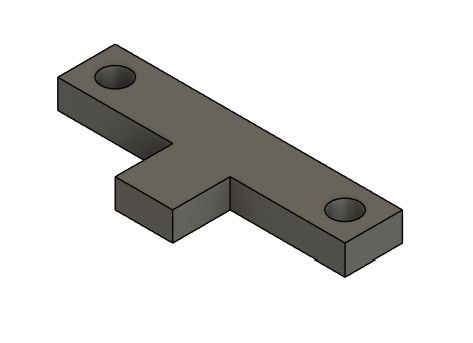
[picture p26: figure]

Obrázek 4.12: Strkutura která slouží na stlačení tlačítka OMORON pro motor 4 - Výkres Příloha V

20


Obrázek 4.13: Struktura pro motor 5 - Výkres Příloha m5 VIII

### 4.5 Struktura pro Motor 5

V této části robota můžeme vidět strukturu na držení motoru 5 viz. 4.13. Na tuto část

přijde na upevnění motoru v místě část kterou můžeme vidět na obrazku 4.14. Tlacitko

OMORON bude připojene z venku na straně a stlačovat ho bude struktura pro motor 6.

### 4.6 Struktura pro Motor 6

V této části můžeme vidět finálni osu. Motor je upevněn v struktuře viz. 4.15 a ze zhora

strukturou 4.16. Tato osa tlačítko nemá, ortože je to výstupní osa na kterou si uživatel

bude moci upevnit cokoliv dle zájmu.

21


Obrázek 4.14: Struktura pro udržení motoru 5 - Výkres Příloha VII


Obrázek 4.15: Strktura pro motor 6 - Výkres Příloha IX

22


Obrázek 4.16: Struktura pro udržení motoru 6 - Výkres Příloha X

23

## Závěr

Cílem mé práce bylo vymodelovat a sestavit šestiosého kolaborativní průmyslového ro-

bota.

Práce mi přinesla mnoho užitečných zkušeností a praxe. Naučil jsem se jak pracovat s

Autodesk Fusion 360 a zlepšit se v Autodesk Inventor.

Samozřejmě jsem se taky naučil jaké chyby už nedělat. V modelování jsem měl hodně

problémy s tolerancema a třením. S komponenty jsem spokojený a práce s nima byla

jednoduchá, jediný problém u komponent jsem měl s šroubama, protože některé díry jsem

namodeloval moc úzké. Každou z částí robota jsem modeloval minimálně dvakrá, protože

jsem vždy našel nějaký způsob jak to vylepšit nebo jsem si našel chybu a potřeboval jsem

ji vylepšit.

Při pracovaní na této práci jsem si velice rozvinul kretivní myšlení a přemýšlení nad

řešením různých problémů. Nejsložitější bylo vymýšlení umístění tlačítek. Výsledný design

můžete vidět na 4.17.

24


Obrázek 4.17: Celý robot - Jarvis

25

## Seznam obrázků

3.1 Uvodní menu Autodesk Fusion 360 s otevřeným projektem, v tomto případě ´

je to model šestiosého kolaborativního robota | 12

3.2 Uvodní menu Autodesk Inventro když je odevřený výkres, v tomto případě ´

je otevřený výkres součásti šestiosého kolaborativního robota | 13
4.1 Podlozka M1 - Výkres Příloha XI | 15
4.2 Lozisko M1 - Výkres Příloha I | 15
4.3 PodlozkaM2 s místem pro motor 2 - Výkres Příloha XII | 16
4.4 Rameno s úchytem na tlacitko - Výkres Příloha XV | 16
4.5 Rameno s úchytem na motor 3 - Výkres Příloha XIII | 17
4.6 Chlazení pro motor 3 - Výkres Příloha IV | 17
4.7 Přední část uchycení motoru 3 - Výkres Příloha III | 18
4.8 Zadní část úchytu pro motor 3 - Výkres Příloha II | 18

4.9 Model na způsob jakým budou spojeny ramena - Výkres Příloha XVI . . . 19

4.10 Podložka/rameno pro motor 4 - Výkres Příloha XIV | 19
4.11 Horní část motoru 4 s výstupem pro kabely - Výkres Příloha VI | 20

4.12 Strkutura která slouží na stlačení tlačítka OMORON pro motor 4 - Výkres

Příloha V | 20
4.13 Struktura pro motor 5 - Výkres Příloha m5 VIII | 21

26

4.14 Struktura pro udržení motoru 5 - Výkres Příloha VII | 22
4.15 Strktura pro motor 6 - Výkres Příloha IX | 22
4.16 Struktura pro udržení motoru 6 - Výkres Příloha X | 23
4.17 Celý robot - Jarvis | 25

Zdroj: Vlastní

27

## Bibliografie

Autodesk (2025a). Autodesk Fusion. url: https://www.autodesk.com/cz/products/

fusion-360/overview?term=1-YEAR&tab=subscription (https://www.autodesk.com/cz/products/fusion-360/overview?term=1-YEAR&tab=subscription) (cit. 28. 04. 2025).

— (2025b). Autodesk Inventor. url: https://www.autodesk.com/products/inventor/

overview (https://www.autodesk.com/products/inventor/overview) (cit. 28. 04. 2025).

Botland (2025). Pružná hliníková spojka 5x8mm. url: https://botland.cz/prvky-pro-

stavbu-3d-tiskaren/18932-pruzna-hlinikova-spojka-5x8mm-5904422355005. html (https://botland.cz/prvky-pro-stavbu-3d-tiskaren/18932-pruzna-hlinikova-spojka-5x8mm-5904422355005.html) (cit. 28. 04. 2025).

Conquest entertainment (2025). Krokový motor NEMA SX17-1003LQCEF, 0,3Nm. url:

https://com.cqe.cz/krokovy-motor-nema-sx17-1003-0-3nm/ (cit. 28. 04. 2025).

LDO MOTORS CO. (2012). Hybrid Stepper Motor LDO-42STH47-1684A(AGF). url:

https://www.solarbotics.com/wp- content/uploads/ldo- 42sth47- 1684a.pdf (https://www.solarbotics.com/wp-content/uploads/ldo-42sth47-1684a.pdf) (cit. 06. 12. 2012).

OMORON (2025). Subminiature Basic Switch. url: https://www.laskakit.cz/user/

related_files/omron_en-ss.pdf (https://www.laskakit.cz/user/related_files/omron_en-ss.pdf) (cit. 28. 04. 2025).

UMAX (2025). Krokový motor NEMA SX17-1005LQCEF, 0,5Nm. url: https://www.

umax.cz/krokovy-motor-nema-sx17-1005lqcef-0-5nm/ (cit. 28. 04. 2025).

28

## Přílohy

Příloha I - DeskaM2

Příloha II - M3 zad

Příloha III - m3 top

Příloha IV - CHLAZENIM3

Příloha V - M4 tlac

Příloha VI - M4 top

Příloha VII - M5

Příloha VIII - m5 base

Příloha IX - M6 top

Příloha X - M6

Příloha XI - MotorPod

Příloha XII - PodlozkaM2

Příloha XIII - Ramenom3

Příloha XIV - ramenom4

Příloha XV - Rameno T

Příloha XVI - SpojR

I

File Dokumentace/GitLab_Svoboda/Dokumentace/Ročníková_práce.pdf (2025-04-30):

## Vyšší odborná škola

## a Střední průmyslová škola elektrotechnická

## Plzeň, Koterovská 85

## ROCNˇ ÍKOVA PR ´ ACE ´

### Téma:

# Model průmyslového šestiosého robota

Autor práce: | Matěj Svoboda
Třída: | 3.L

## Vedoucí práce: Jiří Svihla ˇ

Dne: | 30. 4. 2025

## Hodnocení:

V Plzni dne: 29. 11. 2024 | Mgr. Jan Syřínek, v.r. Zástupce ŘŠ, zástupce statutárního orgánu Vedoucí organizace VOŠ, SŠ, DM

## Vyšší odborná škola a Střední průmyslová škola elektrotechnická Plzeň, Koterovská 85

## Z A D Á N Í R O Č N Í K O V É P R Á C E

Školní rok | 2024/ 2025
Studijní obor | 78 – 42 – M/01 Technické lyceum
Jméno a příjmení | Matěj Svoboda
Třída | 3.L
Předmět | Kybernetika
Hodnoceno v předmětu | Kybernetika
Téma | Model průmyslového šestiosého robota
Obsah práce | Pendant – Návrh a realizace uživatelského rozhraní pro řízení průmyslového robota. • Výběr komponentů (20.12.24) • Prototyp pendantu (24.1.25) • Připojení pendantu k softwaru robota (28.2.25) • Tvorba dokumentace (28.3.25)
Zadávající učitel Příjmení, jméno | Švihla Jiří
Termín odevzdání | 30. dubna 2025

## Obsah

1 Uvod ´ | 6
2 Cíle | 7
3 Komponenty | 8
4 Využitý software | 10
5 Komunikace | 13

6 3D model | 15
7 Kód | 16
Závěr | 19
Seznam příloh: | 22

## Anotace a poděkování

Přes mojí ročníkovou práci jsem se zabýval tvorbou zařízení pro jednoduché ovládání

modelu průmyslového robota. Hlavním cílem bylo vytvořit jednoduchý, ale spolehlivý

design z běžných komponentů. Ostatní díly průmyslového robota dělali Daniel Hornek a

Tomáš Kubín.

Chtěl bych poděkovat YouTube kanálu Cheapcontrols za jejich rozsáhlou knihovnu tutoriálů o Nextion displejích, vedoucímu práce Jiřímu Svihlovi za doporučení Nextion dis- ˇ

plejů a podporu při zpracování této ročníkové práce.

Prohlašuji, že jsem tuto práci vypracoval samostatně a použil literárních pramenů a informací,

které cituji a uvádím v seznamu použité literatury a zdrojů informací.

Prohlašuji, že jsem nástroje UI využil v souladu s principy akademické integrity a že na

využití těchto nástrojů v práci vhodným způsobem odkazuji.

Nesouhlasím s využitím mé práce učiteli VOS a SP ˇ | SE Plzeň k výuce. ˇ
V Plzni dne 30. 4. 2025 | Podpis: |

## 1 Uvod ´

V rámci této ročníkové práce jsem se zaměřil na návrh a realizaci ovládacího zařízení

– pendantu – pro model průmyslového robota. Hlavním cílem bylo vytvořit kompaktní,

spolehlivé a uživatelsky přívětivé zařízení, které umožní jednoduché ovládání robota v

různých provozních podmínkách.

Práce zahrnovala nejen výběr vhodných hardwarových komponentů, ale i návrh vlastního

plošného spoje, programování mikrokontroléru, tvorbu uživatelského rozhraní na doty-

kovém displeji a návrh ochranného krytu pomocí 3D modelování.

6

## 2 Cíle

Cílem projektu bylo vytvořit kompaktní, přenosné a uživatelsky přívětivé zařízení, které

umožní operátorům jednoduše ovládat a nastavovat robota v různých provozních podmínkách.

### 2.1 Hardwarové cíle

Hlavním cílem hardwarové části bylo navrhnout ergonomický a odolný ovládací panel (pendant), který bude vhodný pro použití v náročném průmyslovém prostředí a zároveň

mohl být . Pendant měl být kompaktní, umožňovat pohodlné ovládání jednou rukou a

zároveň integrovat spolehlivé snímání pohybů joysticku pro plynulé řízení všech šesti os

robota. Součástí návrhu bylo také začlenění fyzických tlačítek pro rychlou navigaci v

uživatelském prostředí.

### 2.2 Softwarové cíle

V oblasti softwaru bylo cílem vyvinout program pro mikrokontrolér Raspberry Pi Pico, který by zajišt’oval rychlou a spolehlivou komunikaci mezi pendantem a řídicím systémem

robota. Bylo nutné implementovat čtení a zpracování signálů z joysticku i tlačítek. Bylo

také nutné vytvořit

7

## 3 Komponenty

### 3.1 Raspberry Pi Pico W

Jako hlavní řídicí jednotku ovládacího panelu jsem si zvolil mikrokontrolér Raspberry Pi

Pico W.Jedná se o výkonnou desku založenou na dvoujádrovém procesoru ARM Cortex-M0+ s podporou bezdrátového připojení Wi-Fi [2]. Výběr této komponenty byl motivován

její univerzálností, jednoduchou integrací a cenovou dostupností. Velkou výhodou byla

rovněž rozsáhlá komunitní podpora. Rozhodujícími faktory pro volbu této desky bylo

dostatečné množství vstupně-výstupních pinů pro ovládací prvky a nízká spotřeba energie.

Osobně jsem využil jen programování v MicroPythonu, ale deska podporuje programování i v jazycích Arduino IDE a C/C++.

Deska Raspberry Pi Pico je napájena pomocí přívodu z řídící skříně přes pin VSYS.

Pin VSYS na Raspberry Pi Pico slouží jako vstup napájení, který přijímá širší rozsah

vstupního napětí než standardní USB port.

Využity jsou oba UART kanály, první pro komunikaci s displejem, který využívá pinů 1 (GP0) a 2 (GP1). Druhý kanál je využíván ke komunikaci s řídící skříní a využívá tím

piny 6 (GP4) a 7 (GP5).

8

### 3.2 Nextion Intelligent displej

Pro zobrazování uživatelského rozhraní a interaktivní ovládání jsem nechtěl využívat dis-

plej, pro který bych musel samotné prostředí zcela naprogramovat, proto jsem použil

dotykový displej značky Nextion, konkrétně ze série Intelligent. Tato série displejů je

určena i pro náročnější aplikace, kde je požadováno rychlé vykreslování grafiky, pod-

pora pokročilých vizuálních efektů a práce s animacemi. Intelligent displeje mají vlastní procesor a pamět’, což umožňuje zpracování grafického rozhraní přímo na displeji bez

zatěžování hlavního řídicího mikrokontroléru [3]. Díky podpoře větší kapacity paměti je

možné vytvářet rozsáhlé projekty s více stránkami a komplexní grafikou. Výhodou displejů Nextion je také dostupnost vlastního vývojového prostředí (Nextion Editor), které

mi značně usnadnilo tvorbu a správu uživatelského rozhraní.

Displej je samotný programovatelný jen v jazyce C, jeho editor mi ale umožnil se progra-

mování skoro vyhnout, jediné, co jsem musel programovat, byl výběr stránek pomocí a

posílání dat přes Nextion protokol.

Displej je stejně jako deska napájen přes VSYS na Raspberry Pi Pico, kterým je přiváděno

napětí z řídící skříně.

9

## 4 Využitý software

Při realizaci své ročníkové práce – ovládacího panelu pro model průmyslového robota –

jsem si pečlivě vybíral návrhové programy s ohledem na jejich vhodnost k jednotlivým

částem projektu.

### 4.1 Nextion editor

Pro návrh uživatelského rozhraní na dotykovém displeji jsem využil software Nextion

Editor. Tento program je určen výhradně k tvorbě grafického rozhraní pro displeje Nextion. Nabízí přehledné prostředí pro umist’ování a konfiguraci grafických prvků, jako jsou

tlačítka, textová pole, posuvníky a grafy [1]. Mezi hlavní přednosti editoru patří intui-

tivní ovládání, možnost náhledu výsledného rozhraní přímo v editoru a jednoduchá správa více stránek (obrazovek) v rámci jednoho projektu 4.1.Díky těmto vlastnostem jsem mohl

snadněji a efektivněji vytvořit uživatelské rozhraní bez nutnosti hlubšího programování.

### 4.2 Thonny

Pro programování mikrokontroléru jsem si zvolil integrované vývojové prostředí Thonny.

Jedná se o jednoduché a přehledné IDE 4.2, které je vhodné zejména pro začínající

programátory, ale nabízí i dostatečné možnosti pro složitější projekty. V rámci práce

jsem v Thonny využíval jazyk MicroPython, který je optimalizován pro mikrokontroléry

a umožňuje efektivní správu vstupně-výstupních zařízení. Oproti jiným prostředím jsem

našel v Thonny výhodu v intuitivním rozhraní a snadném nahrávání kódu do zařízení.

10


Obrázek 4.1: Prostředí Nextion editoru s otevřeným projektem [Zdroj: Vlastní]

Obrázek 4.2: Prostředí Thonny s rozpracovaným projektem [Zdroj: Vlastní]

11

### 4.3 Autodesk Inventor

Pro 3D modelování ochranných částí ovládacího panelu jsem využil software Autodesk

Inventor. Tento program jsem si zvolil především proto, že s ním běžně pracujeme v

hodinách průmyslové grafiky a designu, a mám s ním tudíž praktické zkušenosti. Inventor

pro mne nabízel hlavně tvorbu sestavy, do které jsem mohl importovat moji PCB desku,

abych mohl zkontrolovat, jestli vše je na správném místě.

### 4.4 KiCad

Pro návrh elektroniky jsem si vybral KiCad, protože je to volně dostupný open-source

program, který nabízí všechny potřebné funkce pro návrh schémat i plošných spojů 4.3.

Oproti jiným profesionálním nástrojům je zdarma a přitom umožňuje velmi detailní a

přesné návrhy, včetně generování 3D náhledů desek. Díky široké komunitě jsem také

snadno našel návody a podporu.


Obrázek 4.3: Uvodní prostředí Kicad s výběrem jednotlivých funkcí [Zdroj: Vlastní] ´

12

## 5 Komunikace

### 5.1 Komunikace Raspberry Pi Pico s Nextion displejem

Raspberry Pi Pico komunikuje s Nextion dotykovým displejem přes rozhraní UART (sériová linka). Pico odesílá textové příkazy (například změnu hodnoty na displeji, aktuali-

zaci textu) a zároveň přijímá data o událostech (například stisknutí tlačítka). Každý příkaz

zaslaný z Pico na Nextion je ukončen třemi bajty 0xFF 0xFF 0xFF, což je požadavek protokolu Nextion displejů [1].

Displej Nextion při interakci (stisk tlačítka) automaticky pošle přes UART specifickou

sekvenci dat, kterou Pico přijme a analyzuje: Pokud se zjistí, že šlo o stisk určitého tlačítka,

nastaví se v programu příznak, že dané tlačítko bylo aktivováno. Joystick je snímán přes analogové vstupy (ADC) a jeho poloha je periodicky posílána zpět na displej, aby uživatel

viděl aktuální hodnoty.

### 5.2 Komunikace pendantu s řídící skříní

Pendant a řídicí skříň komunikují přes rozhraní UART. Pendant odesílá řídicí skříni data

o poloze joysticku a stavech tlačítek a přijímá od ní instrukce nebo data pro aktualizaci

svého displeje.

Data o poloze joysticku jsou získávána pomocí ADC převodníků, které převádějí analo-

gové signály z joysticku na digitální hodnoty. Tyto hodnoty jsou následně zpracovány a

odesílány přes UART.

Stavy tlačítek na pendantu jsou detekovány jako digitální vstupy. Při stisku nebo uvolnění

tlačítka se odešle odpovídající signál přes UART do řídicí skříně.

Rídicí skříň interpretuje přijatá data a provádí příslušné akce. Může také odesílat zpět data ˇ

13 na pendant, například textové příkazy pro aktualizaci informací na displeji pendantu. Pro

zajištění spolehlivé komunikace se používají protokoly, které definují formát odesílaných dat a způsob jejich zpracování na obou stranách. Pro podrobnější informace se obrat’te

na práci Tomáše Kubína, ve které je tento protokol vysvětlen v sekci 4.1.


Obrázek 5.1: Diagram komunikace [Zdroj: Vlastní]

14

## 6 3D model

Pro ochranu vnitřních prvků pendantu jsem se rozhodl navrhnout ochrannou krabičku.

Snažil jsem se, aby byl její design co nejvíce modulární – proto jsem ji rozdělil na horní

a dolní část. Tento přístup umožňuje v případě poruchy snadnou výměnu jakéhokoliv

jednotlivého prvku bez nutnosti měnit celé zařízení.

Krabičku jsem navrhoval podle rozměrů plošného spoje (PCB), aby bylo uvnitř dosta-

tek místa pro všechny součásti a zároveň zůstala zachována kompaktnost konstrukce.

Pro ověření přesnosti návrhu jsem si PCB naimportoval do programu Autodesk In-

ventor. Následně jsem vytvořil sestavu, kde jsem spojil obě části krabičky společně s

deskou plošných spojů 6.1, abych mohl zkontrolovat správné usazení všech komponentů

a případně doladit drobné detaily.


Obrázek 6.1: Sestava s plošným spojem [Zdroj: Vlastní]

15

## 7 Kód

### 7.1 Main.py

Tento program je určen pro mikrokontrolér Raspberry Pi Pico W, který komunikuje s

dotykovým displejem Nextion přes UART. Kód inicializuje spojení, nastaví tři fyzická

tlačítka a joystick, jehož pohyby snímá pomocí analogových vstupů. Po spuštění proběhne

kalibrace joysticku pro přesné určení středové polohy. Program také připraví Nextion

displej – nastaví výchozí stránku a resetuje hodnoty zobrazených prvků.

V hlavní smyčce se průběžně čtou aktuální hodnoty joysticku a aktualizují se na displeji.

Sleduje se stav fyzických tlačítek a jakékoli změny se ihned promítnou i na Nextion displej.

Současně se přijímají události z dotykových tlačítek na displeji a podle potřeby se vyvolají odpovídající akce. Program tedy zajišt’uje plynulou interakci mezi fyzickými prvky,

joystickem a dotykovým rozhraním, a umožňuje snadné ovládání celého systému. 7.1

### 7.2 NextionProstredi.hmi

Prostředí na displeji, jde rozdělit na hlavní stránku 7.2, ve které jsou tlačítka vedoucí k

stránkám s dostupnými motory za pomocí funkce page. Stránky s motory obsahují jméno

motoru, rotaci motorů, pokud je zapnutý nebo vypnutý homing k ose a pokud je motor

povolen se otáčet. Na stránkách motorů je také tlačítko pro úpravu rotace a tlačítko, které

zavede uživatele zpět na hlavní stránku 7.3.

16


Obrázek 7.1: Diagram programu Main.py [Zdroj: Vlastní]

Obrázek 7.2: Hlavní stránka prostředí ukazjící dostupné motory [Zdroj: Vlastní]

17


Obrázek 7.3: Stránka motoru 1 [Zdroj: Vlastní]

18

## Závěr

Cílem této práce bylo vytvořit ovládací zařízení pro model průmyslového robota.

Jako nováček v oblasti elektrotechniky jsem s výsledkem zařízení spokojený. Samozřejmě

se během práce objevily chyby, například špatný výběr některých komponentů, které

musely být následně nahrazeny, což vedlo k mírnému navýšení nákladů. Tyto chyby však

měly jen malý dopad na finální produkt a do budoucna vím, jak podobným problémům

lépe předcházet.

Díky této práci jsem získal mnoho nových zkušeností, zejména při návrhu vlastní desky

plošných spojů v programu KiCAD a také při seznamování s produkty Nextion.

19

## Seznam obrázků

4.1 Prostředí Nextion editoru s otevřeným projektem [Zdroj: Vlastní] | 11
4.2 Prostředí Thonny s rozpracovaným projektem [Zdroj: Vlastní] | 11
4.3 Uvodní prostředí Kicad s výběrem jednotlivých funkcí [Zdroj: Vlastní] . . . ´ | 12
5.1 Diagram komunikace [Zdroj: Vlastní] | 14
6.1 Sestava s plošným spojem [Zdroj: Vlastní] | 15
7.1 Diagram programu Main.py [Zdroj: Vlastní] | 17
7.2 Hlavní stránka prostředí ukazjící dostupné motory [Zdroj: Vlastní] | 17
7.3 Stránka motoru 1 [Zdroj: Vlastní] | 18

20

## Bibliografie

[1] Cheap Controls. Nextion Displays. Online; citováno 28. dubna 2025. Vydáno: 2020-

2025. url: https://www.youtube.com/playlist?list=PLGOjlGENB8gXVvR9ke2SgF0XTT1dBWmhv.

[2] Gareth Halfacree. The Official Raspberry Pi Beginner’s Guide. Online; citováno
28. dubna 2025. Raspberry Pi Press: Raspberry Pi Press, říj. Vydáno: 2023. isbn:

9781912047277, 1912047276.

[3] Nextion. Intelligent Series Introduction. Online; citováno 28. dubna 2025. Vydáno:

2025. url: https://nextion.tech/intelligent-series-introduction/.

21

## Seznam příloh:

Příloha I: Schéma zapojení

Příloha II: Výkres spodní části krabičky

Příloha III: Výkres horní části krabičky

Příloha IV: KiCad projekt

Příloha V: Kód

22

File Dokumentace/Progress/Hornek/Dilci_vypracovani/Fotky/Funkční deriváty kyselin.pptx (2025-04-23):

## Funkční deriváty kyselin

Chemické vzorce jsou zapsány na papír

## Názosloví

Jestliže nahradíme všechny –OH skupiny v molekule kyseliny halogenem či amidovou skupinou, vznikají funkční deriváty kyselin. Ty to sloučeniny se neřadí do kyselin, jelikož se v jejich molekulách nenachází odštěpitelný atom vodíku.
Halogenid či amidoskupina mají v těchto sloučeninách oxidační číslo I-.

## Názosloví

Názvy jsou tvořeny příslušným halogenidem či aminoskupinou a názvem kyseliny, který je ve 2. pádě. Jestliže se zde nachází více aniontů, jejich názvy upřesníme číslovkovýmí předponami. Kromě názvu kyseliny však můžeme využívat v pojmenování sloučeniny i název příslušné atomové skupiny.

Obsah obrázku text, snímek obrazovky, Písmo, číslo Obsah vygenerovaný umělou inteligencí může být nesprávný.

## Soli karboxylových kyselin

Periodická tabulka prvků

Soli organických kyselin vznikají stejně jako soli anorganických kyselin náhradou jejich kyselého (odštěpitelného) atomu vodíku atomem kovu. Organické kyseliny, které mají ve své molekule více karboxylových skupin, mohou tvořit i hydrogensoli.

## Příprava solí kraboxylových kyselin

CH3COOH + NaOH → CH3COONa + H2O
2CH3COOH + NaOH → 2CH3COONa + CO2 + H2O

- Soli se nejčastěji připravují reakcí karboxylové kyseliny s hydroxidem nebo uhličitanem příslušného kovu

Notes: Oba děje si můžeme demonstrovat na reakci kyseliny octové s hydroxidem a uhličitanem sodným – vzniká octan sodný

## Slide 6

2CH3COOH + Zn → (CH3COO)2Zn + H2

Některé soli organických kyselin lze také připravit reakcí kyseliny s neušlechtilým kovem.

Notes: kyselia octová

## Vlastnosti a význam solí karboxylových kyselin

- Dekaroboxylace:
Reakce, při níž dochází k odstranění karboxylové skupiny. Reakce se provádí tak, že se bezvodá sodná sůl zahřívá s hydroxidem sodným.
Organické kyseliny jsou poměrně slabé, takže
lze z jejich solí vytěsnit anorganickou kyselinu

RCOONa + NaOH → R—H + Na2CO3

Obsah obrázku diagram, řada/pruh, Písmo, Plán Obsah vygenerovaný umělou inteligencí může být nesprávný.

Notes: Vzniká uhlovodík, který obsahuje v molekule o jeden atom uhlíku méně než měla výchozí sůl a uhličitan sodný.
R—H uhlovodík

## Hydrolýza solí

Anionty karboxylových kyselin podléhají snadno hydrolýze. Proto vodné roztoky sodných nebo draselných solí organických kyselin, např. octan sodný, mají zásaditou reakci.
Jak znázorňuje uvedená rovnice, jedná se o rovnovážný děj. Po ustavení rovnováhy je v roztoku obsaženo jisté množství iontů OH⁻, které mu dělují zásaditou reakci

CH3COO⁻ + H2O → CH3COOH + OH⁻

## Využití solí

Chemické vzorce jsou zapsány na papír

Řada solí organických kyselin má praktické využití. Mezi nejvýznamnější patří octan sodný a octan draselný, které slouží jako katalyzátory při tzv. Perkinově syntéze. Octan hlinitý nalezl využití v lékařství při přípravě obkladů. Benzoan sodný je významným konzervačním prostředkem. Sodné a draselné soli vyšších mastných kyselin (stearové a palmitové) se užívají jako mýdla.

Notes: Syntéza organických kyselin z aromatických aldehydů

## Octan draselný

Může být připraven reakcí zásady obsahující draslík, jako např. hydroxidu draselného nebo uhličitanu draselného s kyselinou octovou
2 CH3COOH + K2CO3 → 2 CH3COOK + CO2 H2O
Dá se použít jako odmrazovač. Používá se také jako přídavná látka do potravin jako konzervant nebo regulátor kyselosti. Má schopnost déle zachovat původní přirozenou barvu potravin rost. původu. V medicíně se vyžívá k léčení srdeční arytmie.


## Halogenidy karboxylových kyselin

Halogenidy karboxylových kyselin neboli tzv. acylhalogenidy lze odvodit od organických kyselin náhradou skupiny –OH v karboxylové funkční skupině halogenem. Zbytek kyseliny vzniklý odtržením –OH skupiny se nazývá acyl.
Acylhalogenidy jsou reaktivnější než halogenuhlovodíky, aldehydy nebo ketony. Je tomu tak, protože elektronegativní atom halogenu snižuje elektronovou hustotu na uhlíku karbonylové skupiny více, než je tomu v molekulách aldehydů a ketonů

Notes: Existuje ješte mravenčan draselný, eko sůl

## Příprava

Z acylhalogenidů jsou nejvýznamnější chloridy. Připravují se zahřívaním chloridu fosforitého, fosforečného nebo dichloridu kyseliny siřičité s organickými kyselinami. Z hlediska izolace reakčních produktů je nejvhodnější výchozí látkou thionylchlorid. V průběhu výše popsané reakce kromě acylhalogenidu vzniká oxid siřičitý a chlorovodík, které jsou plynné, a unikají proto z reakční soustavy.

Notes: Dichlorid kyseliny siřičité (thionylchlorid)

## Výroba chloridů

- Pro průmyslové využití byla navržena reakce sodných solí příslušných kyselin s trichloridem kyseliny fosforečné nebo dichloridem kyseliny sírové, které poskytují dobře izolovatelné nejedovaté vedlejší produkty. Jako příklad lze uvést přípravu benzoylchloridu z benzoanu sodného.

Obsah obrázku text, Písmo, diagram, bílé Obsah vygenerovaný umělou inteligencí může být nesprávný.

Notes: trichloridem kyseliny fosforečné – trichloridem fosforylu
Dichloridem kyseliny sírové – dichloridem sulfurylu
Uvedené postupy se využívají i pro přípravu chloridů kyselin obsahujících více karboxylových skupin v molekule

## Vlastnosti a význam

Acylchloridy jsou kapalné, v některých případech i krystalické látky ostrého zápachu, které mají podstatně nižší body varu než kysliny od nichž jsou odvozeny. Jsou velmi reaktivní a v organické syntéze se užívají jako acylační činidla, tedy k zavádění acylskupiny do molekul organických sloučenin.

## Reakce

- S vodou
- S alkoholem
- S amoniakem

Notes: Acylchloridy s vodou za vývoje chlorovodíku a vzniku organické kyseliny
Acyl reagují i s alkoholy a produktem reakce je ester kyseliny a chlorovodík. Obecný mechanizmus této nukleofilně substituční reakce lze popsat touto rovnicí
Mechanizmus nukleofilní substituce probíhá i reakce acylchloridu s amoniakem. Při reakci vzniký amid kyseliny a chlorid amonný

## Benzoylchlorid

Aromatická organická sloučenina, za normálních podmínek se jedná o bezbarvou dýmavou kapalinu dráždivého zápachu. Používá se jako meziprodukt při výrobě barviv, parfémů, org. Peroxidů, léčiv a pryskyřic. l


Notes: C6H5COCl, typ. Acylchlorid, rakce kys benzoové C6H5COOH s chloridem fosforečným

## Estery

Estery jsou významnou skupinou přírodních látek. Vyskytují se například v tucích a olejích. Připravují se tzv. esterifikací, reakcí karboxylové kyseliny s alkoholem.

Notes: Estery karboxylových kyselin

## Fyzikální vlastnosti esterů

Estery jsou kapalné, ojediněle pevné krystalické látky. Zpravidla jsou nerozpustné ve vodě. Estery vřou při teplotě nižší než je bod varu kyseliny, která se na jejich vzniku podílela. Estery totiž, na rozdíl od karboxylových kyselin, nemohou tvořit vodíkové můstky. Pro řadu esterů je charakteristická příjemná vůně, mnohdy připomínající oboce.

## Esterifikace

Probíhá pouze v kyselém prostředí, proto se provádí ze přídavku silné anorganické kyseliny, např. kyseliny sírové. Esterifikace je rovnovážná reakce, její výtěžek lze zvýšit odstraňováním některého z reakčních produktů z reakční směsi. Pokud je reakce katalyzována kyselinou sírovou váže tato kyselina vznikající vodu.

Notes: Příprava esterů karboxylových kyselin
Pokud si pozorně prohlédnete následující rovnici, jistě vám neujde, že ve vzniklém esteru je obsažen kyslíkový atom hydroxylové skupiny alkoholu, zatímco v odštěpené molekule vody je vázán kyslíkový atom původně přítomný v karboxylové skupině kyseliny.

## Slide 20

Prvním krokem esterifikace je protonace karboxylové skupiny kyseliny. Zachycení protonu atomem kyslíku karboxylové skupiny má za následek zvýšení elektronového deficitu na jejím atomu uhlíku a tím také usnadění nukleofilního ataku molekulou alkoholu

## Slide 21

V dalším kroku dochází k vytvoření vazby mezi kyslíkovým atomem hydroxylové skupiny alkoholu a uhlíkovým atomem karboxylové skupiny kyseliny. Následuje odštěpení molekuly vody a protonu.
Tato skutečnost byla prokázána reakcí kyseliny benzoové s methanolem obsahujícím radioaktivní izotop kyslíku

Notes: Dlouhe neřešte

## Příprava esterů

Primární alkoholy tvoří estery snadněji než alkoholy sekundární. Estery terciální alkoholů se tímto způsobem nepřipravují. Pro jejich syntézu se místo karboxylové kyseliny často užívá acylchlorid. Vedlejším produktem reakce je chlorovodík.

Obsah obrázku text, Písmo, bílé, diagram Obsah vygenerovaný umělou inteligencí může být nesprávný.

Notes: Ani fenol většinou netvoří estery přímou esterifikací, ale reaguje s anhydridem příslušné kyseliny. Například fenylester kyseliny octové s připravuje reakcí acetanhydridu s fenolem

## Vlastnosti a význam esterů

- Kyselá hydrolýza
- Alkalická hydrolýza

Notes: Estery v přítomnosti kyselin i hydroxidů podléhají hydrolýze. Kyselou hydrolýzou esterů vzniká alkohol a krabo kys.
Produktem alkalické hydrolýzy esterů je alkohol a sůl kyseliny

## Hydrolýza esterů

Využívá se například při výrobě mýdel. Mýdla a vedlejší produkt reakce – glycerol se získávají alkalickou hydrolýzou esterů vyšších masných kyselin s glycerolem, které jsou hlavní součástí tuků. Kyselou hydrolýzou tuků vznikají vyšší mastné kyseliny a glycerol.

Obsah obrázku text, Písmo, účtenka, řada/pruh Obsah vygenerovaný umělou inteligencí může být nesprávný.

## Reesterifikace

Její mechanismus se podobná hydrolýze esterů. Reakce je katalyzovaná silnou kyselinou, na estery se však nepůsobí vodou, ale jiným alkoholem.

## Nitroglycerin (Glyceroltrinitrát)

Trojnásobný ester alkoholu glycerolu s kyselinou dusičnou. Je to olejovitá bezbarvá až nažloutlá kapalina, která se velmi explozivně rozkládá za uvolnění značného množství energie. V součastnosi je častou surovinou pro výrobu plastických trhavin. V medicíně se využívá k roztažení věnčitých tepen pro snížení krevního tlaku.


## Amidy

Amidy organických kyselin vznikají náhradou -OH skupiny obsažené v karboxylové funkční skupině amidoskupinou –NH2

## Fyzikální vlastnosti

Amidy organických kyselin jsou kapalné nebo krystalické látky, s vysokými body tání a varu. Tato vlastnost je dána přítomností vodíkových můstků mezi jejich molekulami

## Příprava

Výchozími látkami pro přípravu amidů jsou karboxylové kyseliny a většina jejich funkcí derivátů. Amidy se často získávají termický rozkladem amonných solí, které vznikají reakcí kyseliny a amoniakem

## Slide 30

Funkční deriváty karboxylových kyselin lze převést na amidy za mírnějších podmínek než samotné kyseliny, přičemž reaktivita klesá v řadě chloridy, anhydridy a estery. Celý děj lze vyjádřit následující rovnicí

## Polyamidy - nylon

Je synteticky připravené textilní vlákno. Vzniká reakcí diamidu s dikarboxylovou kyselinou. Nylon je první syntetický polymer a první syntetické vlákno, které bylo vyrobeno z uhlí, vody a vzduchu a které mělo komerční úspěch.
Sylonky


## Nitrily

Nitrily jsou organické sloučeniny, které ve svých molekulách obsahují funkční skupiny –C N .

## Vlastnosti

Nitrily jsou jedovaté kapaliny nebo krystalické látky, které vřou při nižší tepoltě než karboxylové kyseliny, od kterých jsou odvozeny. V kyselém i alkalickém prostředí hydrolyzují. Produktem hydrolýzy jsou v závislosti na reakčních podmínkách amidy nebo i samostatné kyseliny.

## Příprava

Alifatické nitrïly se často získávají reakcí kyanidů alkalických kovů s alkylhalogenidy. Tyto reakce patří do skupiny neukleofilních substitucí. Obecný mechanizmus reakce vyjadřuje následující schéma:

## Průmysl

Mezi průmyslově významné nitrily patří akrylonitril. Vyrábí se reakcí propenu s amoniakem a kyslíkem.
Akrylonitril je surovinou pro výrobu syntetických vláken.

2CH2=CH – CH3 + 2NH3 + 3O2 → 2CH2=CH – CN + 6H2O

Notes: akrynitril

## Kyanovodík

Bezbarvá, velmi těkavá kapalina s intenzivním pachem hořkých mandlí.
Je to velmi silný jed, je smrtelný. Toxický účinek spočívá v blokování enzymů tkáňového dýchání. Toxicita však velmi závisí na koncentraci a době působení, i středně vysoké dávky absorbované během desítek minut nebudou mít fatální následky, ovšem jen lehce vyšší koncentrace navodí smrt během jednotek minut.
Je extrémně hořlavý

## Děkuju za pozornost

## Zdroje

Chemie pro čtyřletá gymnázia 3. díl – Aleš Mareček, Jaroslav Honza 1. vydání 2005
https://nazvoslovi.cz/studium/funkcni_derivaty_kyselin

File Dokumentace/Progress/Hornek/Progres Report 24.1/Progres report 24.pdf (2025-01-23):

Progres report 24.1.2025
V složce jsou připojený modely součástí robotu a všechny spojené dohromady. Bohužel zatím je udělaný jen spodní část robota, která je složená z dvou motorů LDO-42STH47-1684, a jednoho spínače (https://www.laskakit.cz/omron-koncovy-spinac-pakovy-5a-125vac/ ). Vše modeluji ve Autodesk Fusion a je to tisknuté na 3D tiskárně. Ramena budu postupně přidávat ale jelikož pracuji s Fusionem poprvé tak to trvá, omlouvám se za zpoždení.

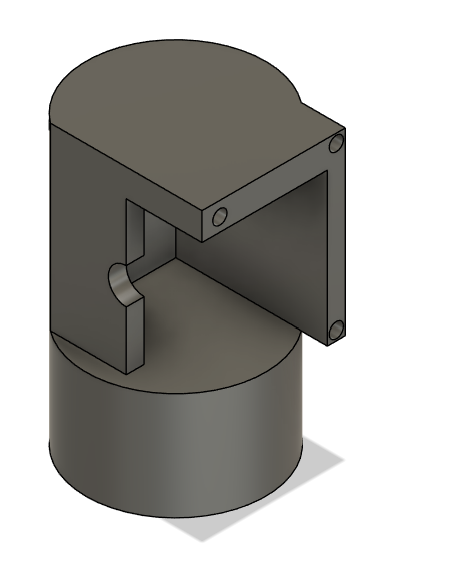
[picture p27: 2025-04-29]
Dokumentace/HORNEK_Dokumentace_30.4.2025/Ročníkovka obrázky/PodlozkaM5.png

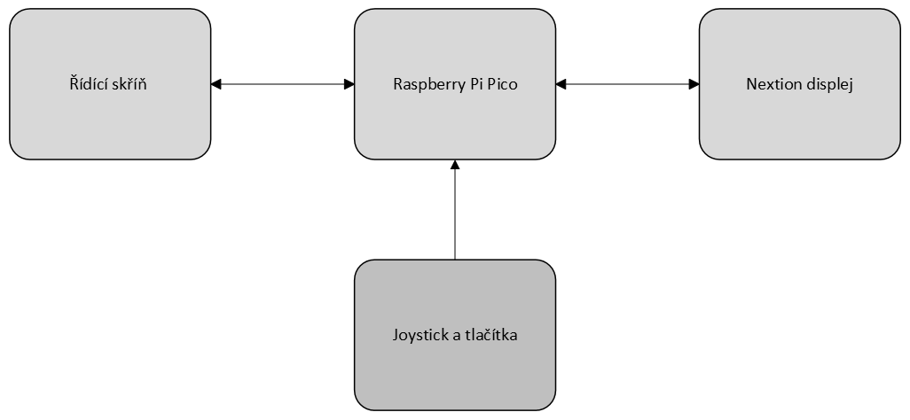
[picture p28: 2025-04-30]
Dokumentace/GitLab_Svoboda/Dokumentace/Obrázky/Diagram_komunikace.png

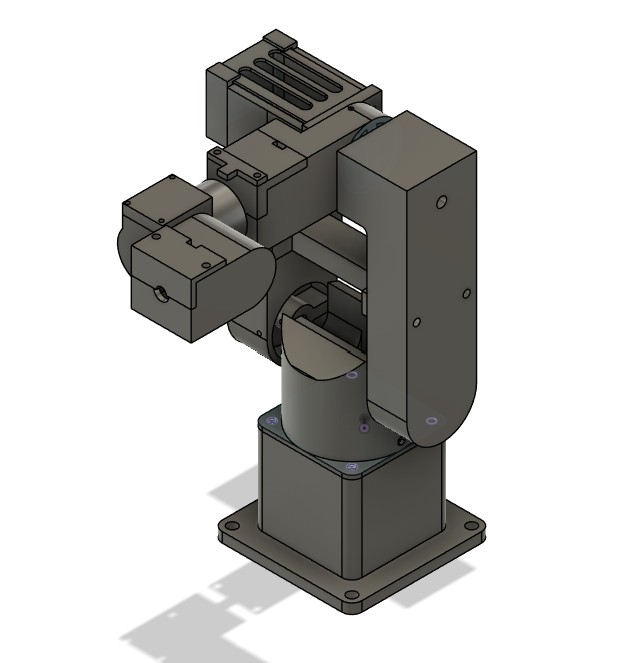
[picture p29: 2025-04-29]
Dokumentace/HORNEK_Dokumentace_30.4.2025/Ročníkovka obrázky/RobotSkladani.png

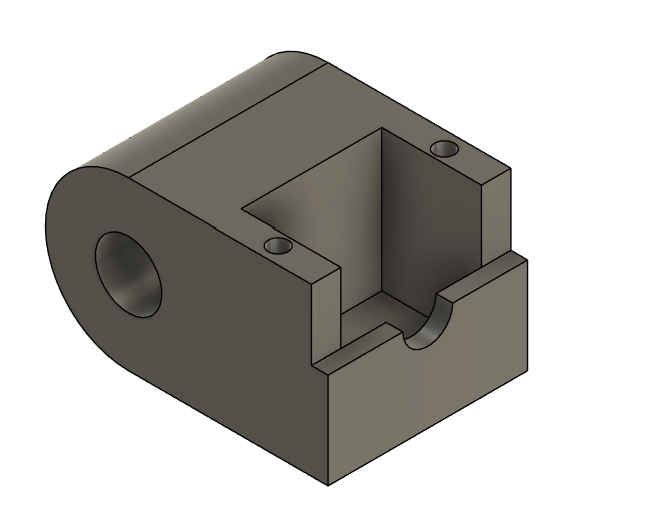
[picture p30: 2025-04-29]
Dokumentace/HORNEK_Dokumentace_30.4.2025/Ročníkovka obrázky/PodlozkaM6.png

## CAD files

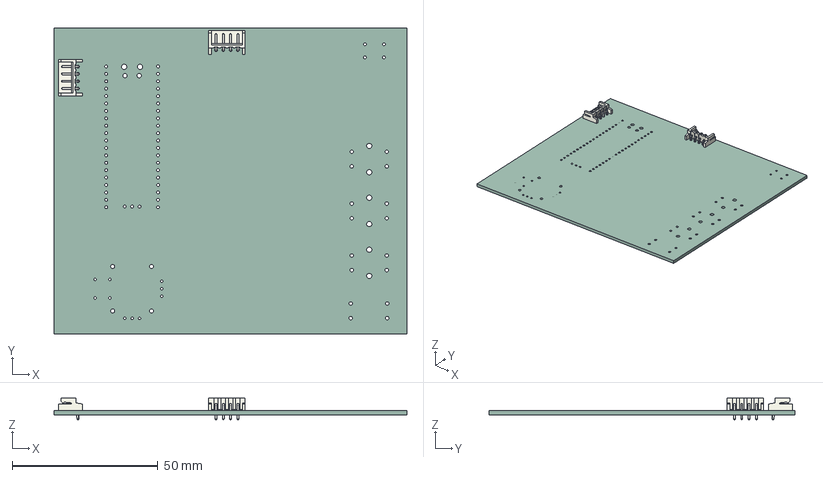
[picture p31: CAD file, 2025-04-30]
Dokumentace/GitLab_Svoboda/Přílohy/Priloha_IV/schema.step
121.0 x 105.0 x 7.40 mm
JST_EH_S4B-EH_1x04_P2.50mm_Horizontal x 2
schema_PCB

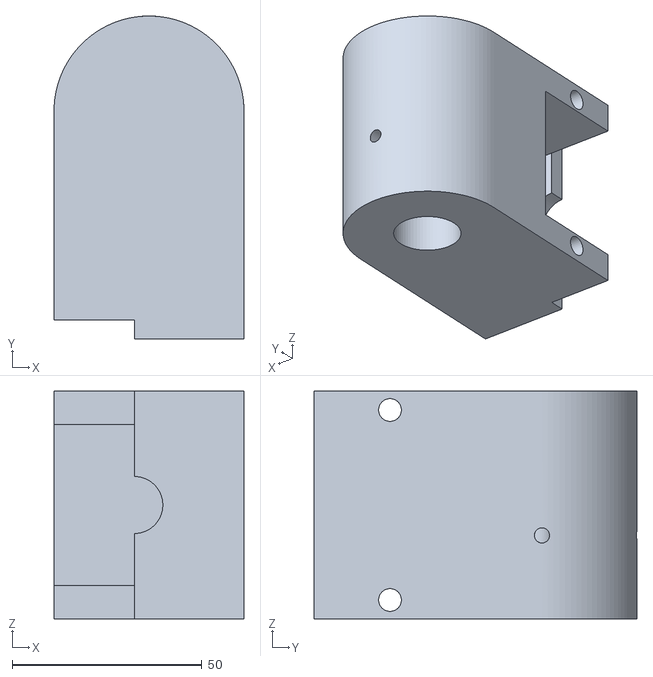
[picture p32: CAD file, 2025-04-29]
Dokumentace/HORNEK_Dokumentace_30.4.2025/Robot - model/m6 v2.stl
50.0 x 85.0 x 60.0

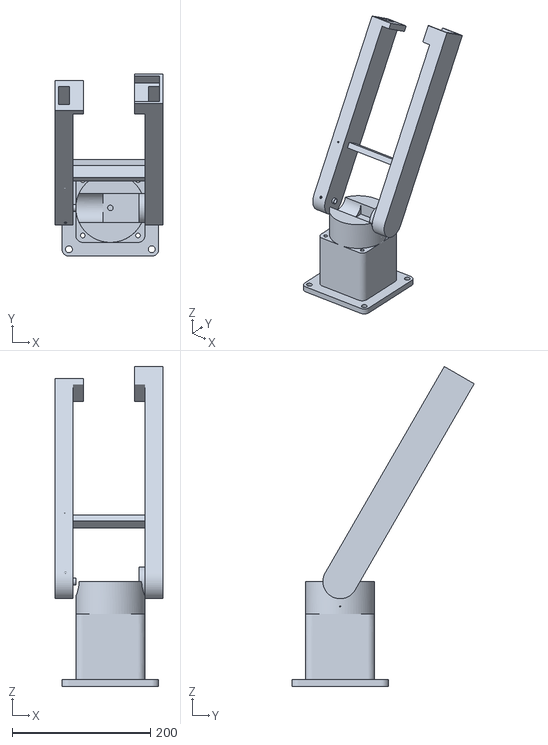
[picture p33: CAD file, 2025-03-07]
Dokumentace/Progress/Hornek/28.2/Robot - skládání v13.stl
156.0 x 264.2 x 463.4

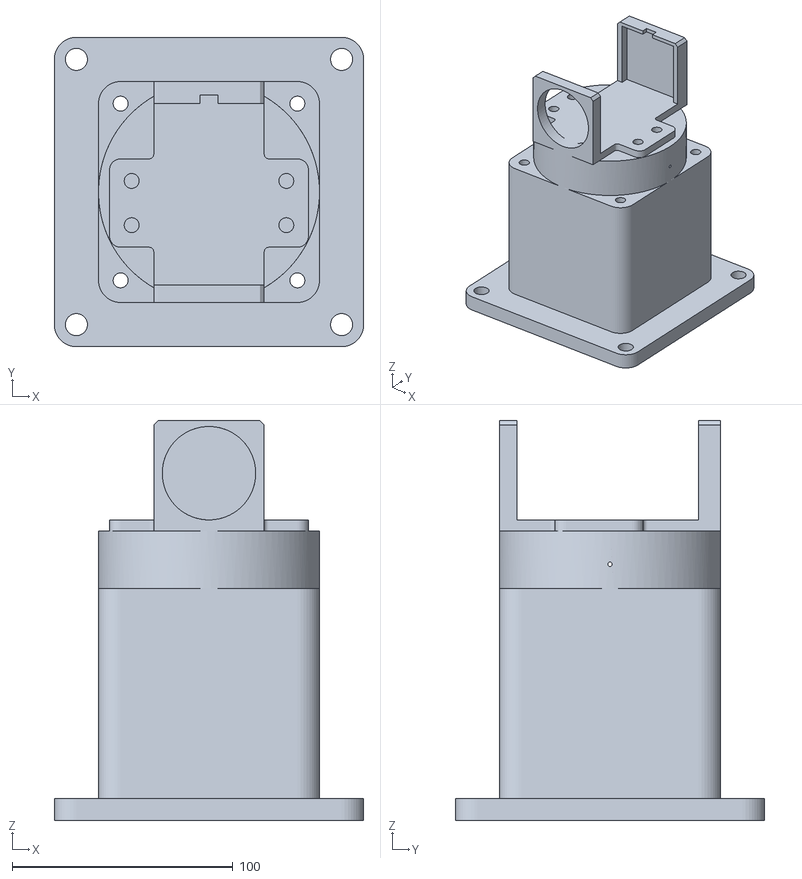
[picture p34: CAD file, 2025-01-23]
Dokumentace/Progress/Hornek/Progres Report 24.1/Robot - skládání_.stl
140.0 x 140.0 x 181.0

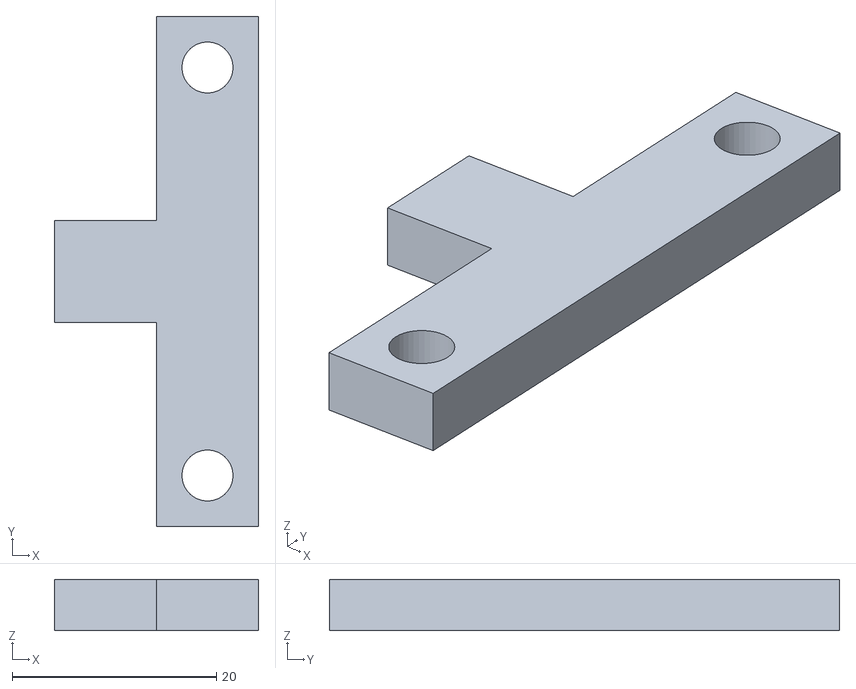
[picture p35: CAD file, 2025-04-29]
Dokumentace/HORNEK_Dokumentace_30.4.2025/Robot - model/m4 tlac v1.stl
20.0 x 50.0 x 5.00

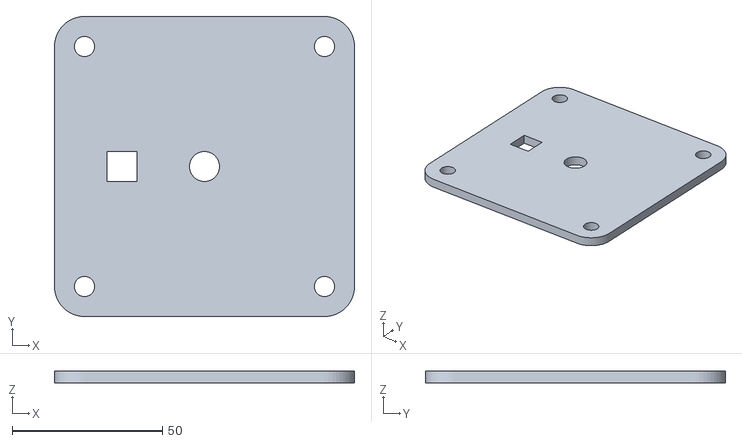
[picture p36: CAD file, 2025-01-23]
Dokumentace/Progress/Hornek/Progres Report 24.1/Deska Top.stl
100.0 x 100.0 x 4.00

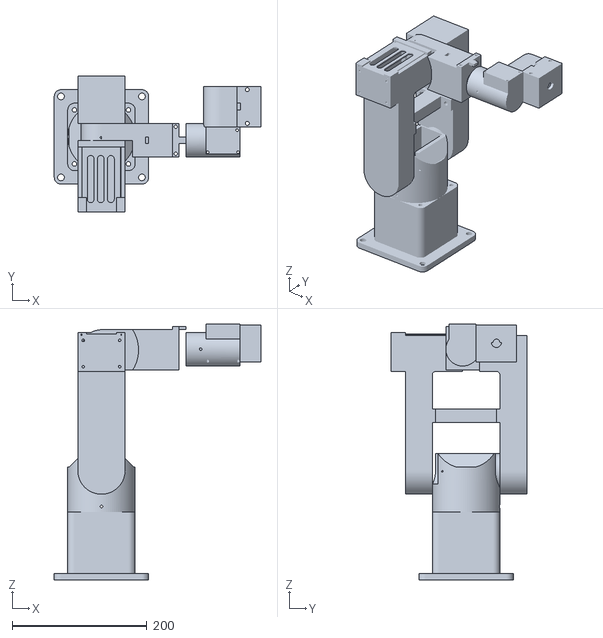
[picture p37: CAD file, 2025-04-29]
Dokumentace/HORNEK_Dokumentace_30.4.2025/Robot - model/RobotCely.stl
306.1 x 201.0 x 379.5

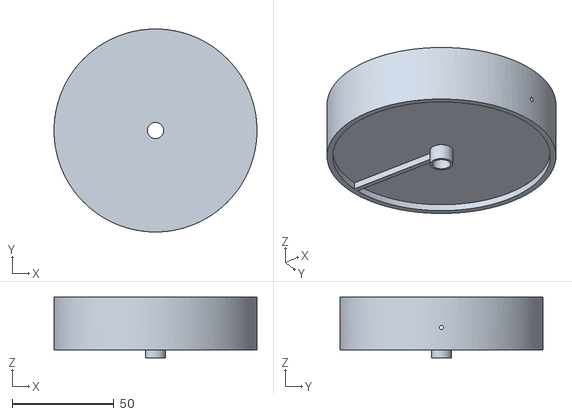
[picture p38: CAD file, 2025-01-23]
Dokumentace/Progress/Hornek/Progres Report 24.1/Podložka pro M2.stl
100.0 x 100.0 x 30.0

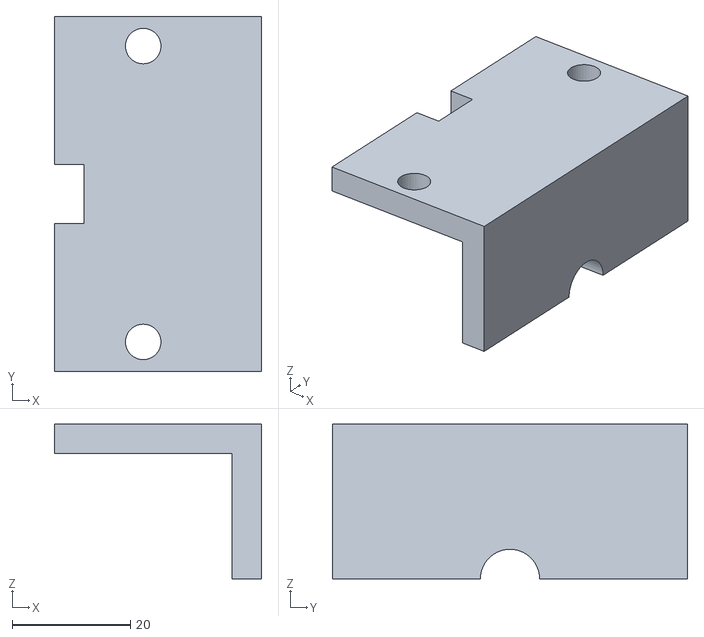
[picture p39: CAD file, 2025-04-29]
Dokumentace/HORNEK_Dokumentace_30.4.2025/Robot - model/m6 top v3.stl
35.0 x 60.0 x 26.1

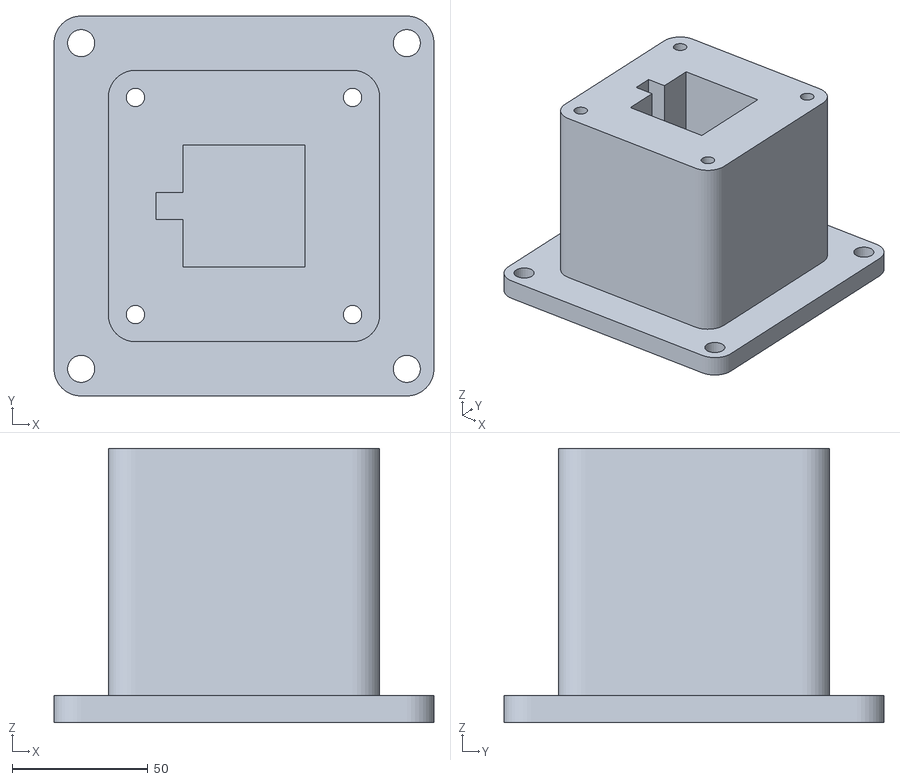
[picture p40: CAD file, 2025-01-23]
Dokumentace/Progress/Hornek/Progres Report 24.1/Deska dole.stl
140.0 x 140.0 x 101.0

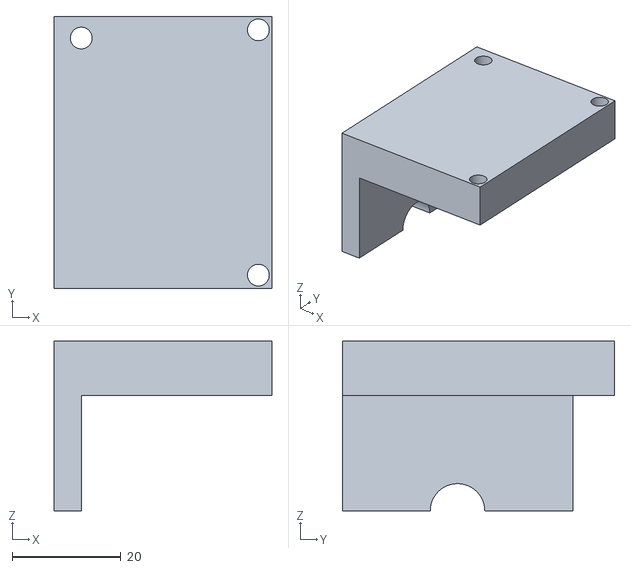
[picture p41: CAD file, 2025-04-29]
Dokumentace/HORNEK_Dokumentace_30.4.2025/Robot - model/m5 v2.stl
40.0 x 50.0 x 31.1

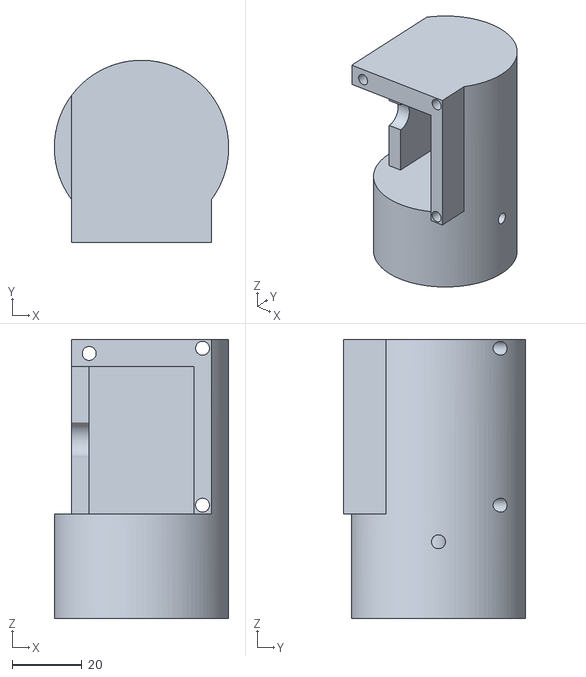
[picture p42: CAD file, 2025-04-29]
Dokumentace/HORNEK_Dokumentace_30.4.2025/Robot - model/m5 yey v1.stl
50.0 x 52.3 x 80.0

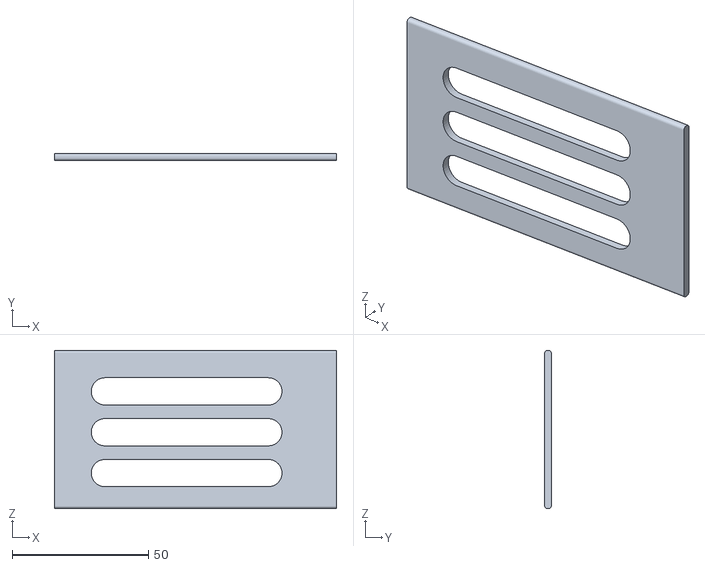
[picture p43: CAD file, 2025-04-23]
Dokumentace/HORNEK_Dokumentace_30.4.2025/Robot - model/chlazení m3 v2.stl
103.5 x 2.50 x 58.0

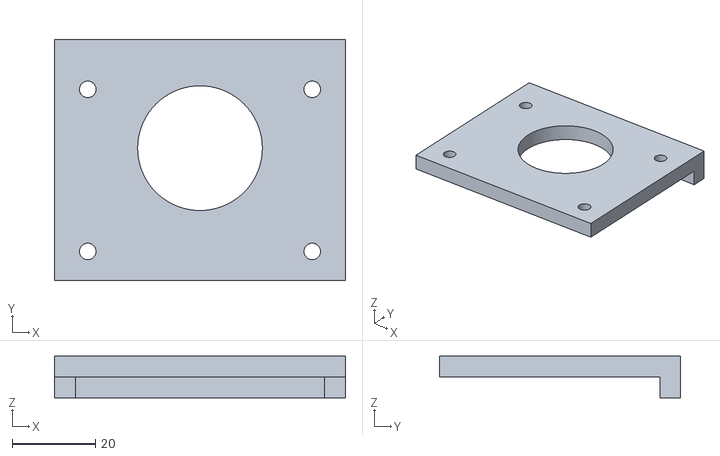
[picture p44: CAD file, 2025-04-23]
Dokumentace/HORNEK_Dokumentace_30.4.2025/Robot - model/m3 v5.stl
70.0 x 58.0 x 10.0

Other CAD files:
Dokumentace/HORNEK_Dokumentace_30.4.2025/Robot - model/podložka m2 yey v8.stl
Dokumentace/HORNEK_Dokumentace_30.4.2025/Robot - model/m4 top v3.stl
Dokumentace/HORNEK_Dokumentace_30.4.2025/Robot - model/Motor1(podložka).stl
Dokumentace/HORNEK_Dokumentace_30.4.2025/Robot - model/rameno tlacitko v4.stl
Dokumentace/GitLab_Svoboda/Přílohy/Priloha_IV/schema/schema/JST_EH_S4B-EH_1x04_P2.50mm_Horizontal.ipt
Dokumentace/GitLab_Svoboda/Přílohy/Priloha_IV/schema/schema/schema.iam
Dokumentace/GitLab_Svoboda/Přílohy/Priloha_IV/schema/schema/schema_PCB.ipt
Dokumentace/HORNEK_Dokumentace_30.4.2025/Robot - model/DeskaProM2.stl
Dokumentace/HORNEK_Dokumentace_30.4.2025/Robot - model/m3 zad v3.stl
Dokumentace/HORNEK_Dokumentace_30.4.2025/Robot - model/rameno m2 spojka v9.stl
Dokumentace/HORNEK_Dokumentace_30.4.2025/Robot - model/rameno v2.stl
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

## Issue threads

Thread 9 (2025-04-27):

Kontrola dokumentace

mandl01, 2025-04-27:
Prosil bych o kontrolu dokumentace. Plus bych se chtěl zeptat, co mám v overleafu špatně, protože mi přijde, že rámečky na stránkách fungují zvláštňe. Přikládám i link na projekt v overleafu https://www.overleaf.com/read/nsfhqdghfywz#ad1225

[Rocnikovka.pdf](https://github.com/user-attachments/files/19931812/Rocnikovka.pdf)

bublinak, 2025-04-28:
Ozvi se na hodině. Některé věci jsou zbytečně rozsáhlé (Pico 2 apod.), jiné zase příliš málo (samotné skripty). Rozvaděč nemá výktery. Schémata budou chtít přiložit. Blokové diagramy (třeba malý vývoják start->boot.py->main.py by se vyjímal, nebo přehledové (blokové) schéma) by se taky vyjímaly. Foto robota by také nevadilo (i když to není přímo tvoje práce). Zmínit v anotaci že pracuješ s dalšími dvěma kolegy. Jinak celkem dobré...

skely, 2025-05-02:
Tohle je asi hotové, že?

Closed 2025-05-02.

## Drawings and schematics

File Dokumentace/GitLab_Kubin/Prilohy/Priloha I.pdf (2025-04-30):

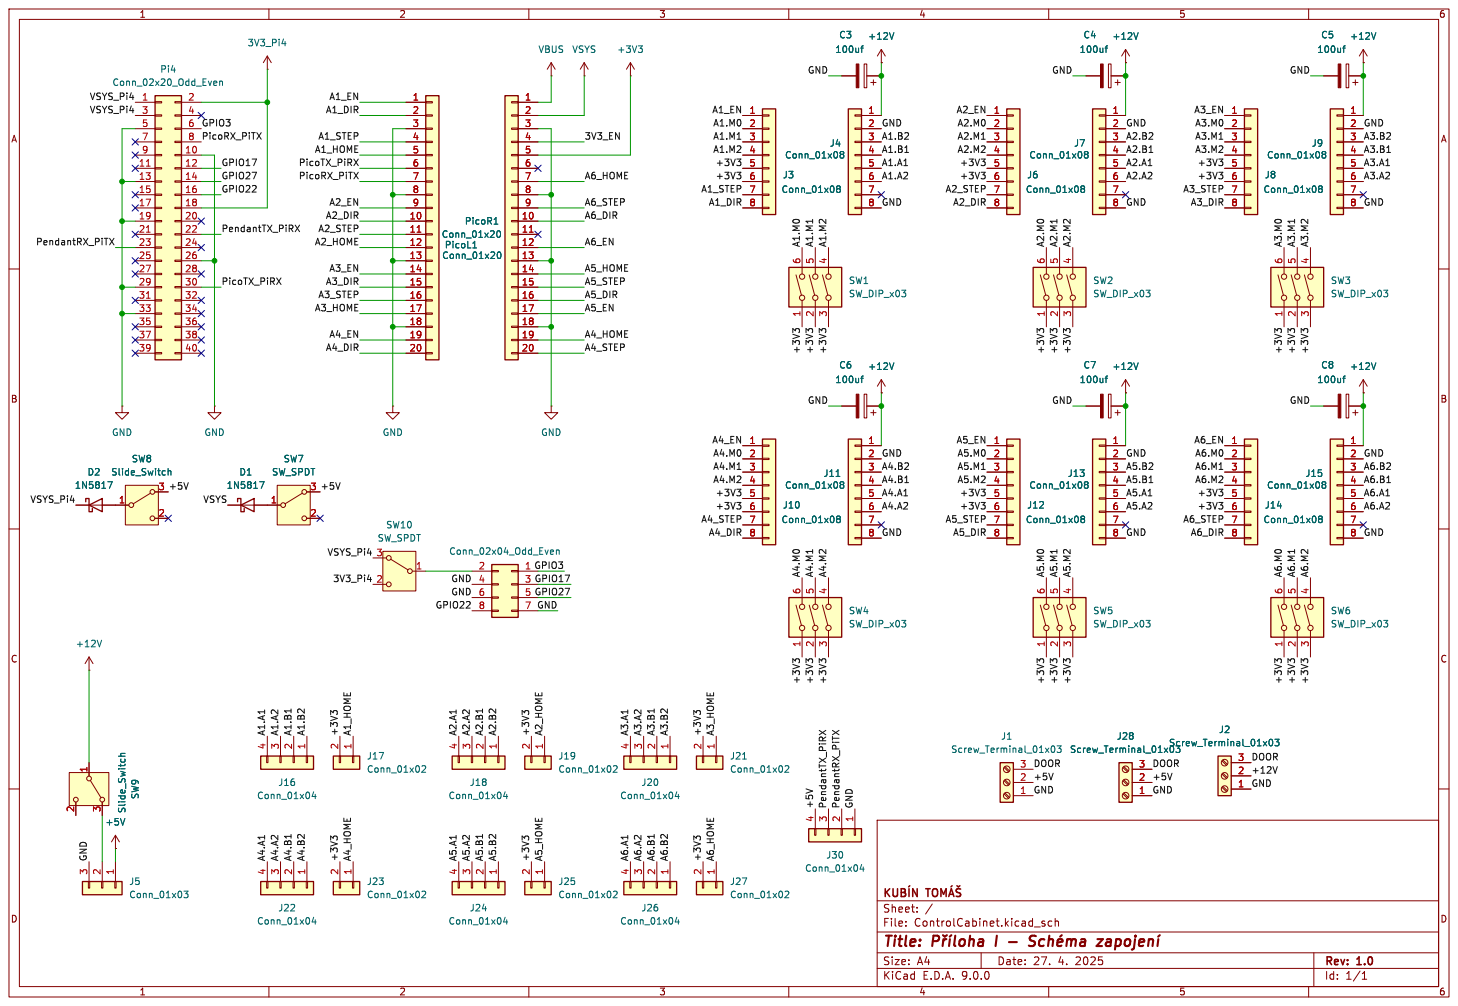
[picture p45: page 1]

Id: 1/1 Title: þÿPYíloha I - þÿSchéma þÿzapojení File: ControlCabinet.kicad_sch Sheet: / þÿKUBÍN þÿTOMÁ`

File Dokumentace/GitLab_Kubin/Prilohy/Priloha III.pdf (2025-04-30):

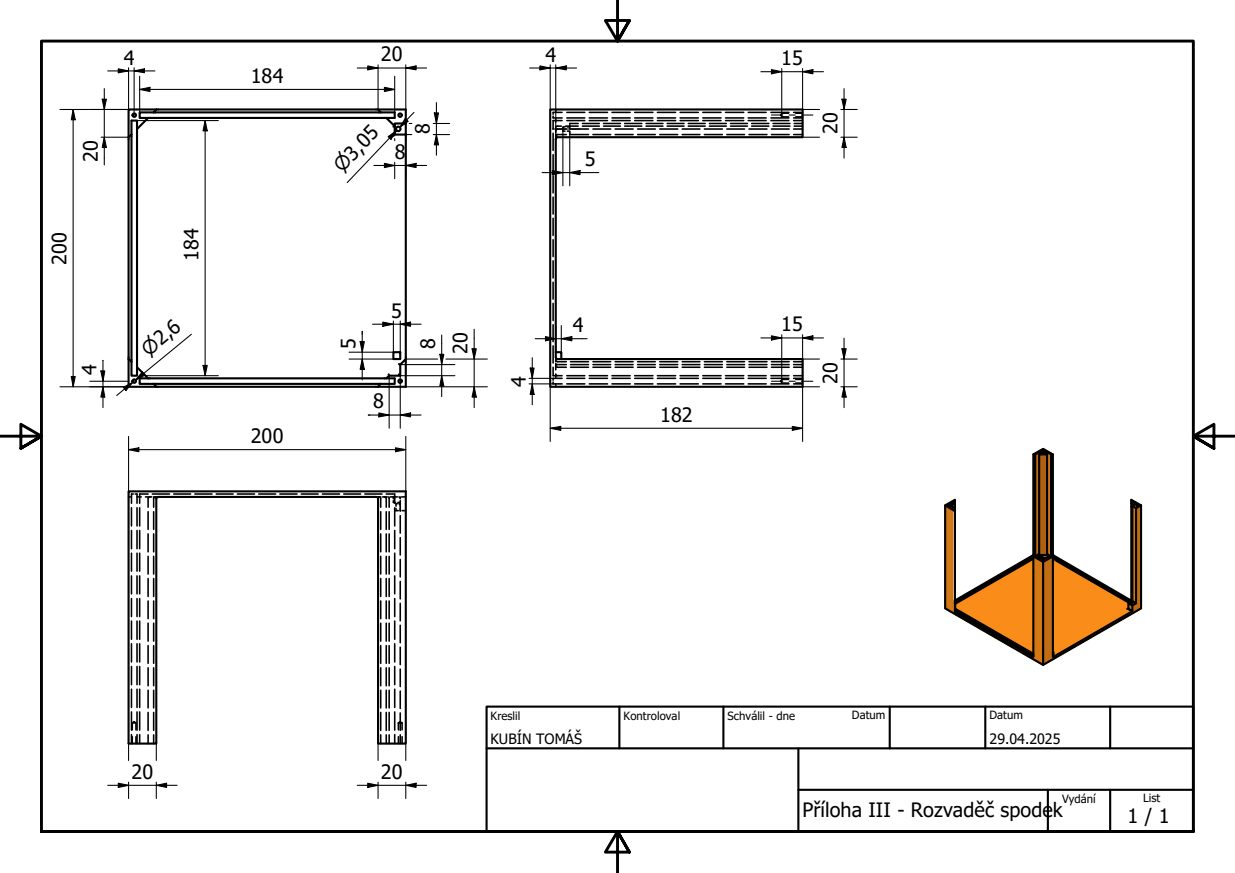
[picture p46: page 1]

Kreslil KUBÍN TOMÁŠ | Kontroloval | Schválil - dne Datum | Datum 29.04.2025

Příloha III - Rozvaděč spodek | Vydání | List 1 / 1

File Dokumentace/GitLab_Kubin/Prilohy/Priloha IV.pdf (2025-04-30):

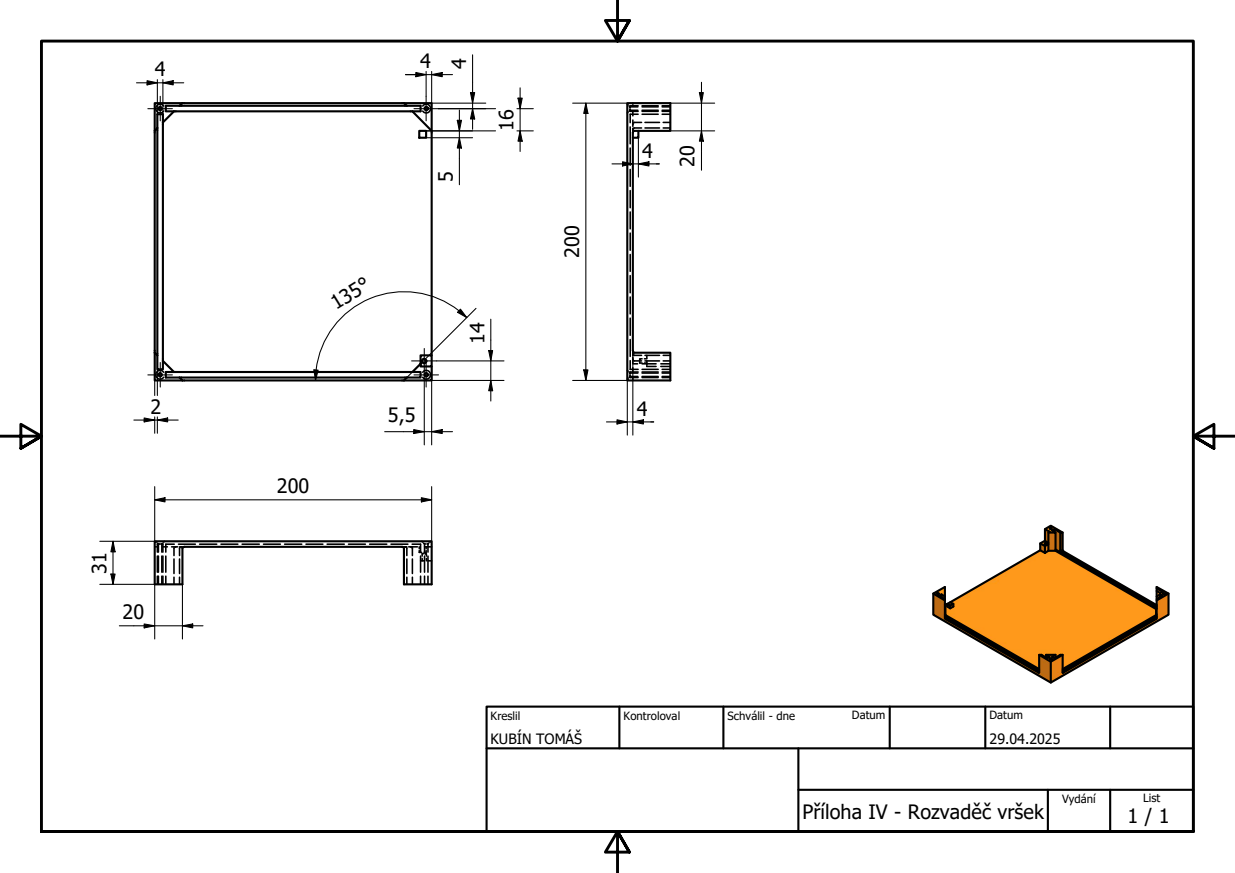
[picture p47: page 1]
KUBÍN TOMÁŠ; Kreslil; Kontroloval; Schválil - dne; Datum

Příloha IV - Rozvaděč vršek

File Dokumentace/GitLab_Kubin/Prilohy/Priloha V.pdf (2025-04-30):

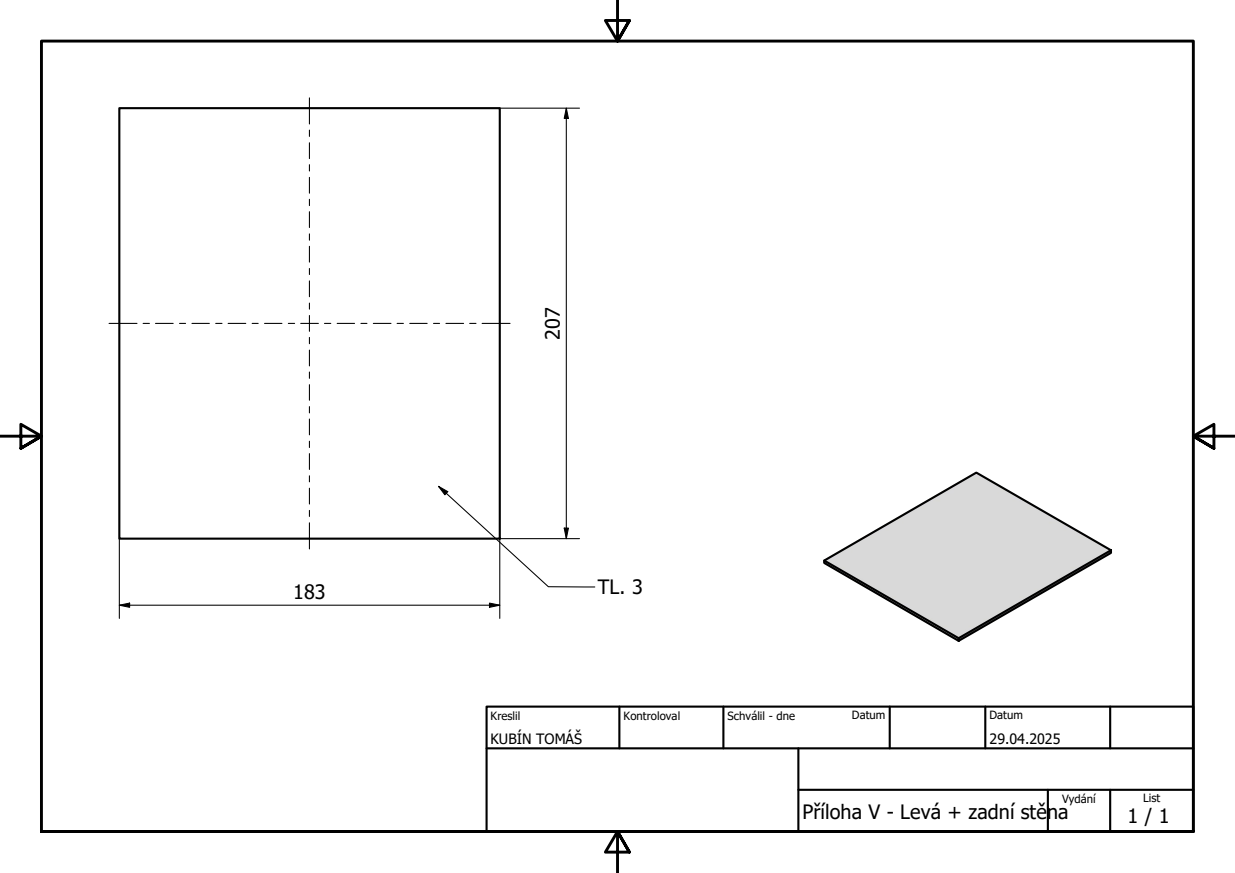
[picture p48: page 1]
KUBÍN TOMÁŠ; Kreslil; Kontroloval; Schválil - dne; Datum

Příloha V - Levá + zadní stěna

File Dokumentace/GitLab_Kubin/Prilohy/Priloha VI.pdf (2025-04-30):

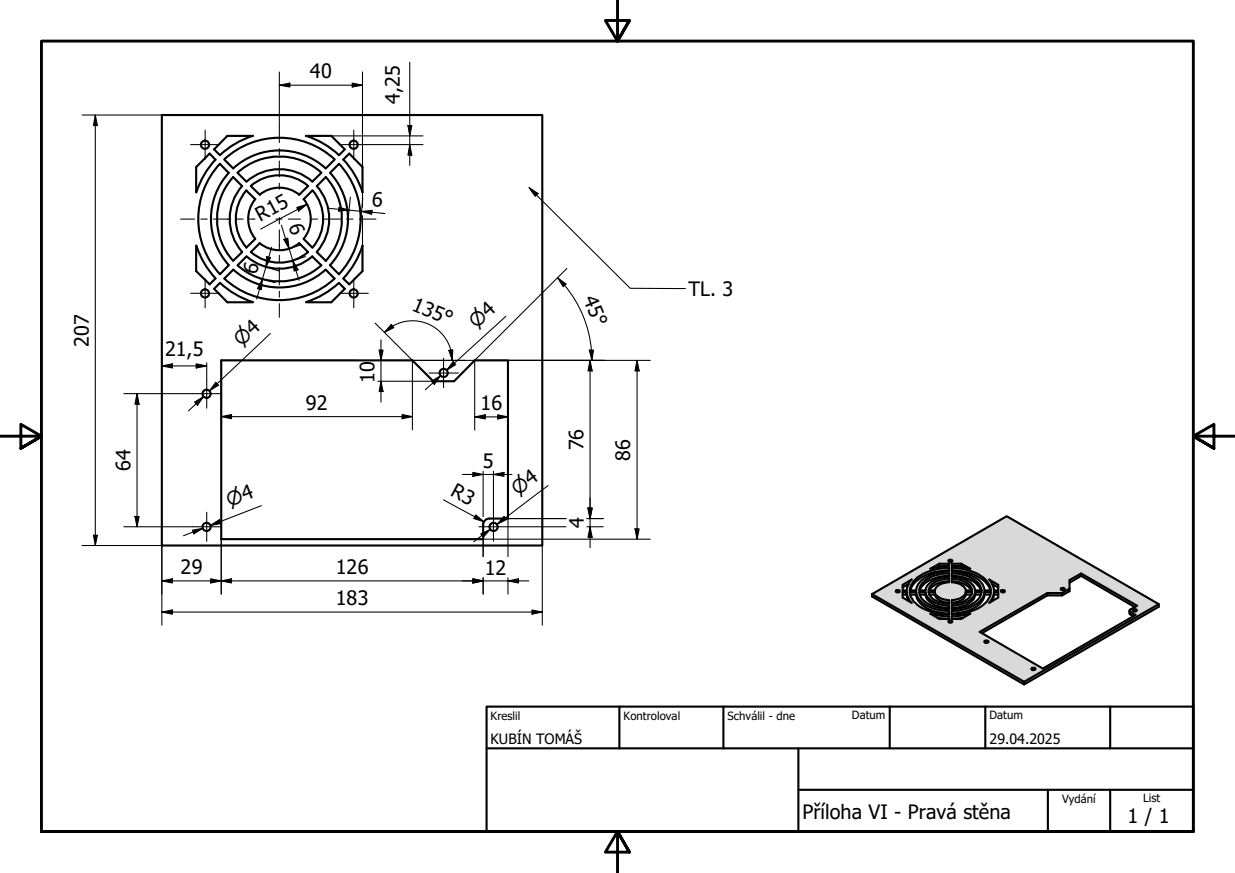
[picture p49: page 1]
KUBÍN TOMÁŠ; Kreslil; Kontroloval; Schválil - dne; Datum

Příloha VI - Pravá stěna

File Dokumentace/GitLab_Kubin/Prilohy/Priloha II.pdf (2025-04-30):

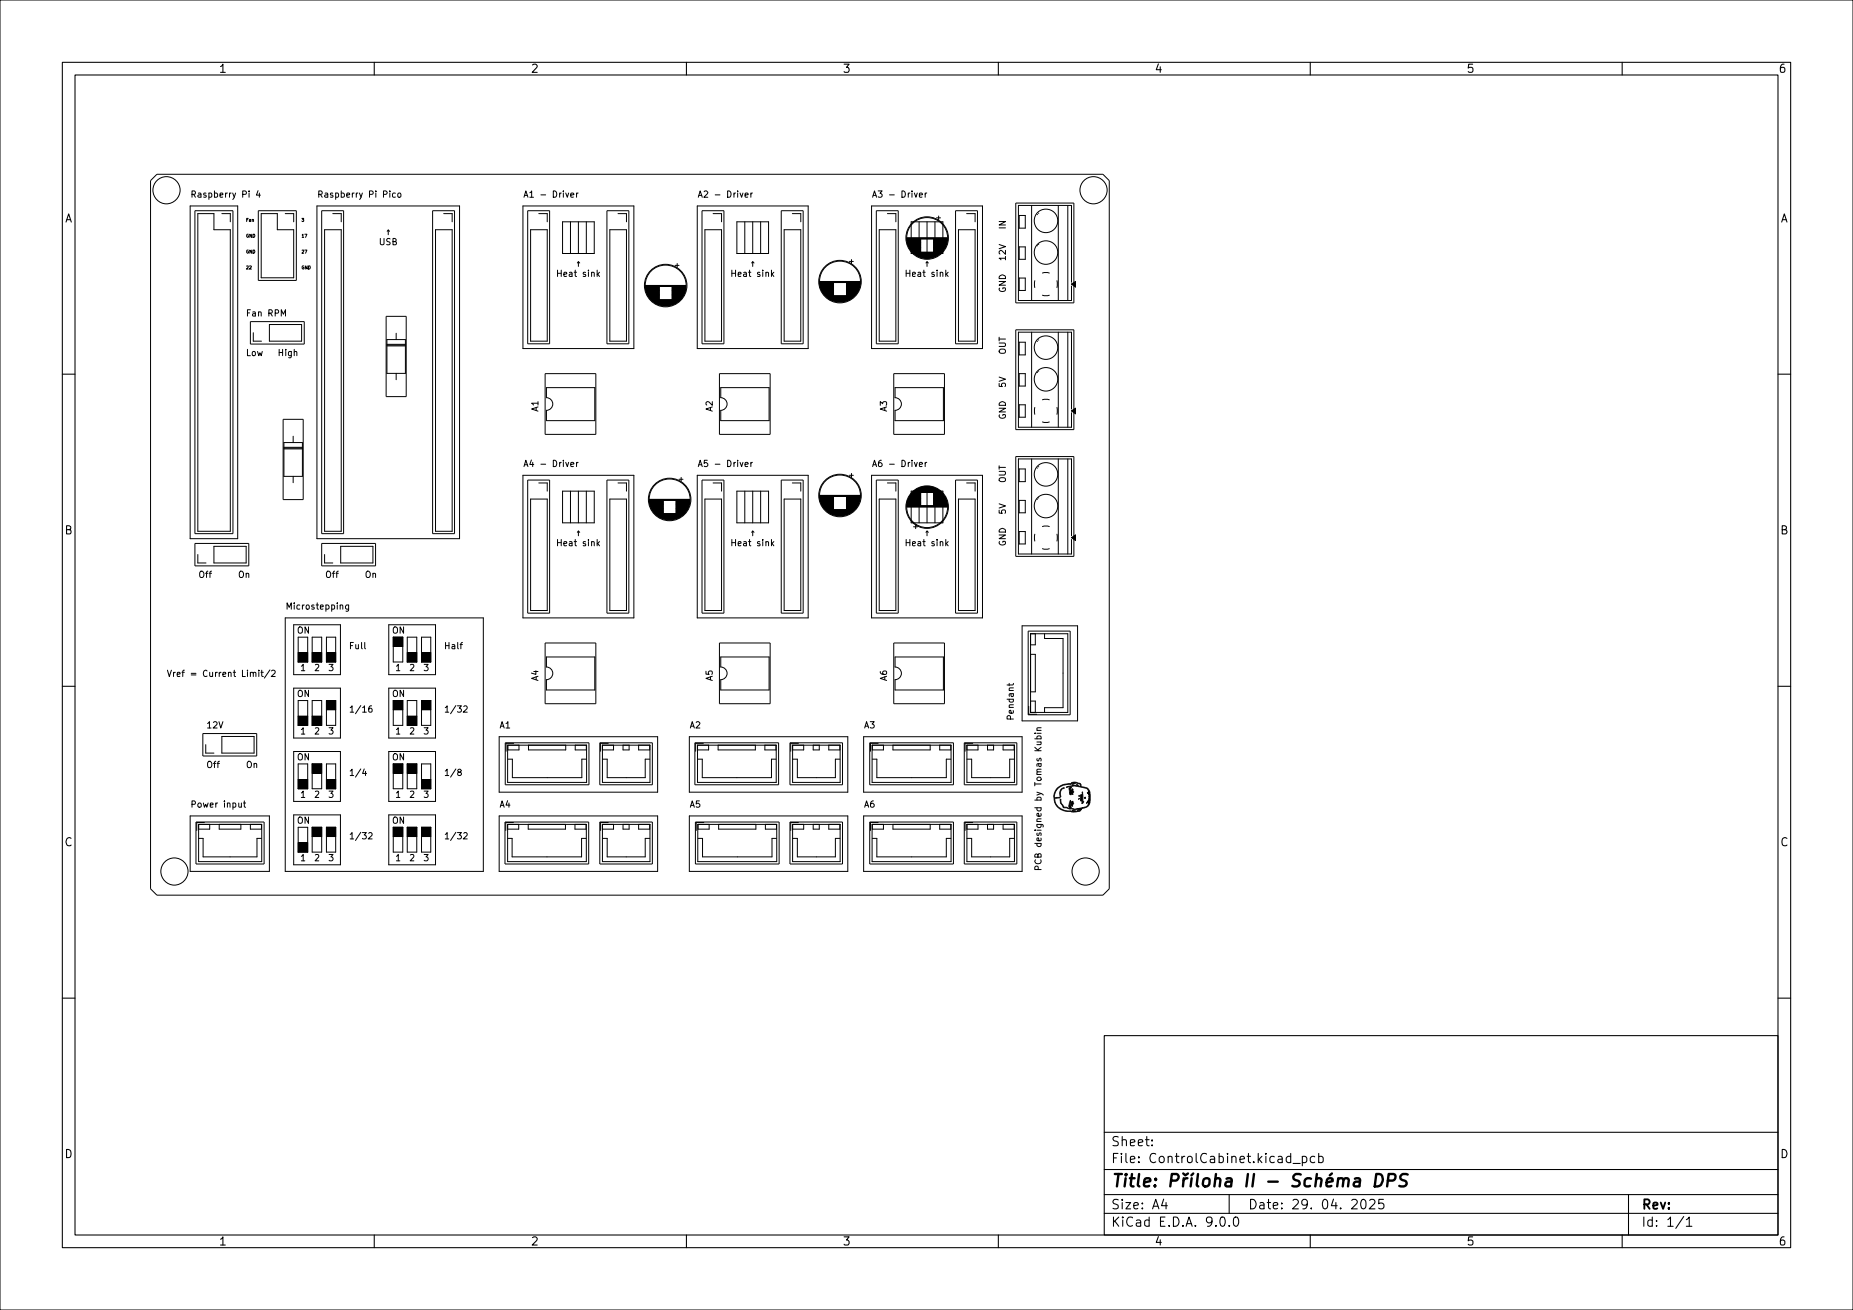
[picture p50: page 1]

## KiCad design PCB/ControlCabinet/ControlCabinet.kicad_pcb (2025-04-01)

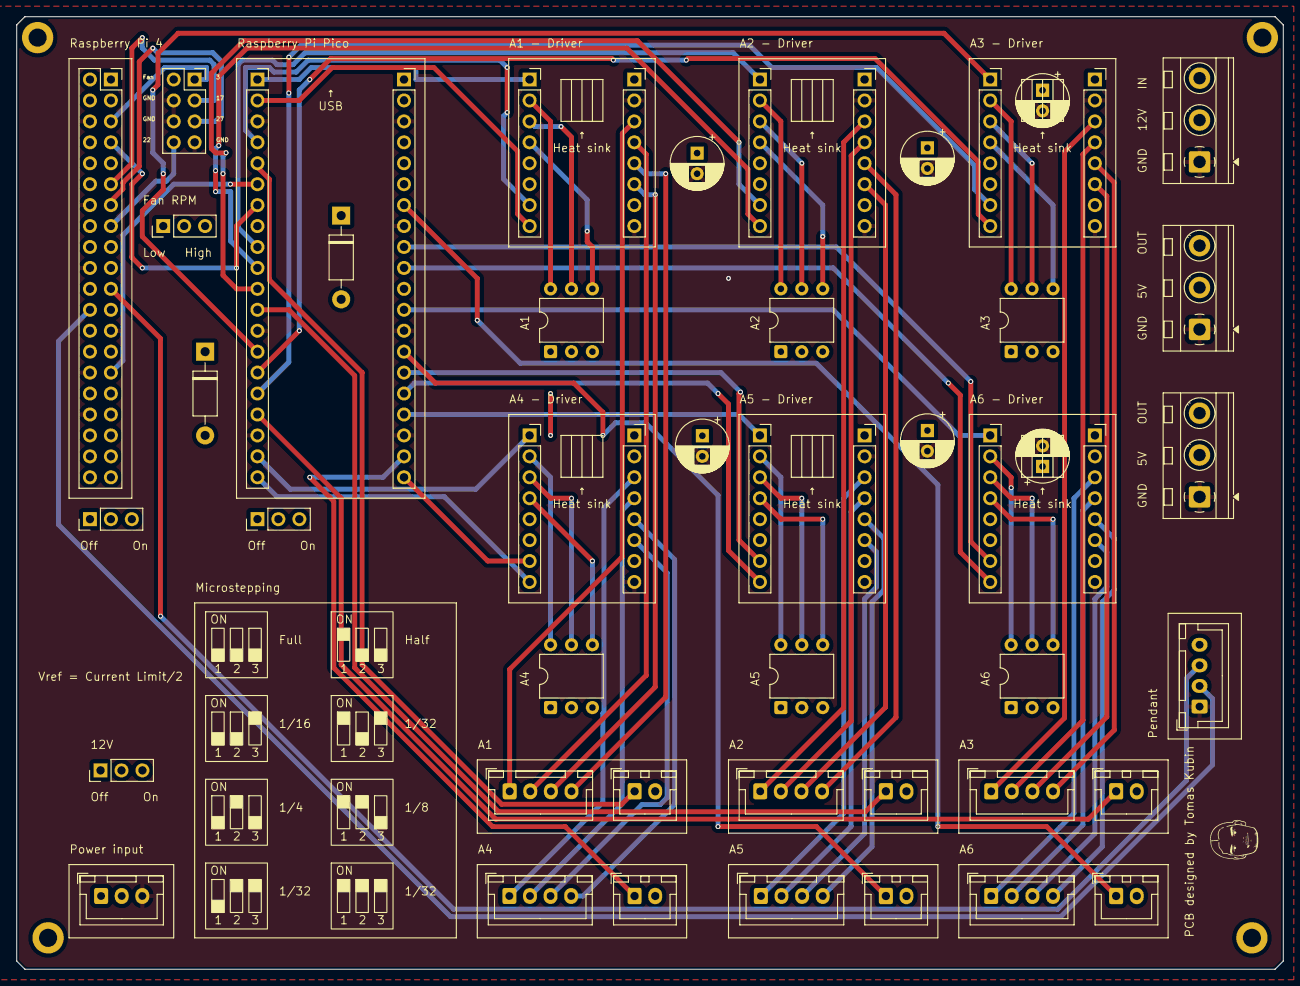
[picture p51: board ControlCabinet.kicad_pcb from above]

Board: 4 copper layers, 153.7 x 115.6 mm, 51 parts (0 on the bottom side), 86 nets.

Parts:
C3, C4, C5, C6, C7, C8: 100uf; CP_Radial_D6.3mm_P2.50mm
D1, D2: 1N5817; D_DO-41_SOD81_P10.16mm_Horizontal
GPIO17: Conn_02x04_Odd_Even; PinSocket_2x04_P2.54mm_Vertical
J1, J2, J28: Screw_Terminal_01x03; TerminalBlock__1x03_P5.08mm_Horizontal
J3, J4, J6, J7, J8, J9, J10, J11, J12, J13, J14, J15: Conn_01x08; PinSocket_1x08_P2.54mm_Vertical
J5: Conn_01x03; JST_XH_B3B-XH-A_1x03_P2.50mm_Vertical
J16, J18, J20, J22, J24, J26, J30: Conn_01x04; JST_XH_B4B-XH-A_1x04_P2.50mm_Vertical
J17, J19, J21, J23, J25, J27: Conn_01x02; JST_XH_B2B-XH-A_1x02_P2.50mm_Vertical
Pi4: Conn_02x20_Odd_Even; PinSocket_2x20_P2.54mm_Vertical
PicoL1: Conn_01x20; PinSocket_1x20_P2.54mm_Vertical
PicoR1: Conn_01x20; PinSocket_1x20_P2.54mm_Vertical
SW1, SW2, SW3, SW4, SW5, SW6: SW_DIP_x03; DIP-6_W7.62mm
SW7, SW10: SW_SPDT; Slide_Switch_1x03_P2.54mm
SW8, SW9: Slide_Switch; Slide_Switch_1x03_P2.54mm

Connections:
3V3_Pi4: Pi4.2, Pi4.18, SW10.2 (C)
+3V3: J3.5, J3.6, J6.5, J6.6, J8.5, J8.6, J10.5, J10.6, J12.5, J12.6, J14.5, J14.6, J17.2, J19.2, J21.2, J23.2, J25.2, J27.2, PicoR1.5, SW1.1, SW1.2, SW1.3, SW2.1, SW2.2, SW2.3, SW3.1, SW3.2, SW3.3, SW4.1, SW4.2, SW4.3, SW5.1, SW5.2, SW5.3, SW6.1, SW6.2, SW6.3
+5V: J1.2, J5.1, J28.2, J30.4, SW7.3 (A), SW8.3 (A)
+12V: C3.1, C4.1, C5.1, C6.1, C7.1, C8.1, J2.2, J4.1, J7.1, J9.1, J11.1, J13.1, J15.1, SW9.1 (B)
/A1.A1: J4.5, J16.4
/A1.A2: J4.6, J16.3
/A1.B1: J4.4, J16.2
/A1.B2: J4.3, J16.1
/A1.M0: J3.2, SW1.6
/A1.M1: J3.3, SW1.5
/A1.M2: J3.4, SW1.4
/A1_DIR: J3.8, PicoL1.2
/A1_EN: J3.1, PicoL1.1
/A1_HOME: J17.1, PicoL1.5
/A1_STEP: J3.7, PicoL1.4
/A2.A1: J7.5, J18.4
/A2.A2: J7.6, J18.3
/A2.B1: J7.4, J18.2
/A2.B2: J7.3, J18.1
/A2.M0: J6.2, SW2.6
/A2.M1: J6.3, SW2.5
/A2.M2: J6.4, SW2.4
/A2_DIR: J6.8, PicoL1.10
/A2_EN: J6.1, PicoL1.9
/A2_HOME: J19.1, PicoL1.12
/A2_STEP: J6.7, PicoL1.11
/A3.A1: J9.5, J20.4
/A3.A2: J9.6, J20.3
/A3.B1: J9.4, J20.2
/A3.B2: J9.3, J20.1
/A3.M0: J8.2, SW3.6
/A3.M1: J8.3, SW3.5
/A3.M2: J8.4, SW3.4
/A3_DIR: J8.8, PicoL1.15
/A3_EN: J8.1, PicoL1.14
/A3_HOME: J21.1, PicoL1.17
/A3_STEP: J8.7, PicoL1.16
/A4.A1: J11.5, J22.4
/A4.A2: J11.6, J22.3
/A4.B1: J11.4, J22.2
/A4.B2: J11.3, J22.1
/A4.M0: J10.2, SW4.6
/A4.M1: J10.3, SW4.5
/A4.M2: J10.4, SW4.4
/A4_DIR: J10.8, PicoL1.20
/A4_EN: J10.1, PicoL1.19
/A4_HOME: J23.1, PicoR1.19
/A4_STEP: J10.7, PicoR1.20
/A5.A1: J13.5, J24.4
/A5.A2: J13.6, J24.3
/A5.B1: J13.4, J24.2
/A5.B2: J13.3, J24.1
/A5.M0: J12.2, SW5.6
/A5.M1: J12.3, SW5.5
/A5.M2: J12.4, SW5.4
/A5_DIR: J12.8, PicoR1.16
/A5_EN: J12.1, PicoR1.17
/A5_HOME: J25.1, PicoR1.14
/A5_STEP: J12.7, PicoR1.15
/A6.A1: J15.5, J26.4
/A6.A2: J15.6, J26.3
/A6.B1: J15.4, J26.2
/A6.B2: J15.3, J26.1
/A6.M0: J14.2, SW6.6
/A6.M1: J14.3, SW6.5
/A6.M2: J14.4, SW6.4
/A6_DIR: J14.8, PicoR1.10
/A6_EN: J14.1, PicoR1.12
/A6_HOME: J27.1, PicoR1.7
/A6_STEP: J14.7, PicoR1.9
/DOOR: J1.3, J2.3, J28.3
/GPIO3: GPIO17.1, Pi4.6
/GPIO17: GPIO17.3, Pi4.12
/GPIO22: GPIO17.8, Pi4.16
/GPIO27: GPIO17.5, Pi4.14
/PendantRX_PiTX: J30.2, Pi4.23
/PendantTX_PiRX: J30.3, Pi4.22
/PicoRX_PiTX: Pi4.8, PicoL1.7
/PicoTX_PiRX: Pi4.30, PicoL1.6
/VSYS_Pi4: D2.1 (K), Pi4.1, Pi4.3, SW10.3 (A)
GND: C3.2, C4.2, C5.2, C6.2, C7.2, C8.2, GPIO17.4, GPIO17.6, GPIO17.7, J1.1, J2.1, J4.2, J4.8, J5.3, J7.2, J7.8, J9.2, J9.8, J11.2, J11.8, J13.2, J13.8, J15.2, J15.8, J28.1, J30.1, Pi4.5, Pi4.10, Pi4.13, Pi4.19, Pi4.26, Pi4.29, Pi4.33, PicoL1.3, PicoL1.8, PicoL1.13, PicoL1.18, PicoR1.3, PicoR1.8, PicoR1.13, PicoR1.18
unnamed: D1.2 (A), SW7.1 (B)
unnamed: D2.2 (A), SW8.1 (B)
unnamed: GPIO17.2, SW10.1 (B)
unnamed: J5.2, SW9.3 (A)
VSYS: D1.1 (K), PicoR1.2

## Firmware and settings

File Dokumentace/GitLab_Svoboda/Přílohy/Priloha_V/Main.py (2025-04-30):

from machine import Pin, UART, ADC
import time
import _thread

uart = UART(0, baudrate=115200, tx=Pin(12), rx=Pin(13))

button1 = Pin(2, Pin.IN, Pin.PULL_UP)
button2 = Pin(3, Pin.IN, Pin.PULL_UP)
button3 = Pin(4, Pin.IN, Pin.PULL_UP)

x_axis = ADC(26)  # GP26
y_axis = ADC(27)  # GP27  

X_CENTER = 32768  
Y_CENTER = 32768  

DEAD_ZONE = 2000  


class Achse:
    def __init__(self):
        self.desPos = 0
        self.curPos = 0
        self.homing = 0
        self.homed = 0
        self.enabled = 0
        self.enabledCMD = 0

A1 = Achse()
A2 = Achse()
A3 = Achse()
A4 = Achse()
A5 = Achse()
A6 = Achse()


def enableListByte(): 
    enableList = 0
    enableList = enableList | A1.enabledCMD
    enableList = enableList | (A2.enabledCMD << 1)
    enableList = enableList | (A3.enabledCMD << 2)
    enableList = enableList | (A4.enabledCMD << 3)
    enableList = enableList | (A5.enabledCMD << 4)
    enableList = enableList | (A6.enabledCMD << 5)
    return enableList



def map_value_with_deadzone(value, center):
    if abs(value - center) < DEAD_ZONE:
        return 50 
    
    if value < center:
        return map_value(value, 0, center - DEAD_ZONE, 0, 49)
    else:
        return map_value(value, center + DEAD_ZONE, 65535, 51, 100)

def map_value(x, in_min, in_max, out_min, out_max):
    return (x - in_min) * (out_max - out_min) // (in_max - in_min) + out_min

def send_to_nextion(command):
    end_cmd = b'\xff\xff\xff'
    uart.write(command.encode() + end_cmd)
    time.sleep(0.05)  
    
    # Vyčistit buffer od odpovědí
    if uart.any():
        uart.read()

def read_joystick():
    
    x_raw = x_axis.read_u16()
    y_raw = y_axis.read_u16()
    
    x_mapped = map_value_with_deadzone(x_raw, X_CENTER)
    y_mapped = map_value_with_deadzone(y_raw, Y_CENTER)
    
    return x_mapped, y_mapped

def calibrate_joystick():
    print("Vycentruj joystick a čekej")
    time.sleep(2)
    
    x_sum = 0
    y_sum = 0
    samples = 10
    
    for _ in range(samples):
        x_sum += x_axis.read_u16()
        y_sum += y_axis.read_u16()
        time.sleep(0.1)
    
    x_center = x_sum // samples
    y_center = y_sum // samples
    
    print(f"Kalibrovaný centr - X: {x_center}, Y: {y_center}")
    return x_center, y_center

def check_uart_for_data():
    """Čtení dat z UART a detekce stisknutí tlačítek"""
    global nextion_button0_active, nextion_button1_active, nextion_button2_active
    global nextion_button3_active, nextion_button4_active, nextion_button5_active
    global nextion_back_button_active
    
    if uart.any():
        data = uart.read()
        
        if data:
            # Hledání standardního vzoru dat z Nextion
            if len(data) >= 7 and data[0] == 0x65:
                component_id = data[2]
                event_type = data[3]
                page_id = data[4]
                
                print(f"Nextion event: component_id={component_id}, event_type={event_type}, page_id={page_id}")
                
            # Pokud používáte starší způsob komunikace nebo vlastní protokol
            # Ponecháme také původní detekci pro kompatibilitu
            for byte in data:
                if byte == 0x01:
                    nextion_button0_active = True
                    print("Detekováno tlačítko 1 z dat UART (jednobajtový kód)")
                elif byte == 0x02:
                    nextion_button1_active = True
                elif byte == 0x03:
                    nextion_button2_active = True
                elif byte == 0x04:
                    nextion_button3_active = True
                elif byte == 0x05:
                    nextion_button4_active = True
                elif byte == 0x06:
                    nextion_button5_active = True
                elif byte == 0x69:  
                    nextion_back_button_active = True
                    print("Detekováno tlačítko ZPĚT z dat UART (jednobajtový kód)")
                    
                elif byte == 0x20: #Enabled/Disabled
                    A1.enabledCMD = not A1.enabledCMD
                elif byte == 0x21: #Homing Enabled/Disabled
                    A1.homing = not A1.homing
                elif byte == 0x22: #A1 Pos +
                    A1.desPos =  A1.curPos + 5
                elif byte == 0x23: #A1 Pos -
                    A1.desPos =  A1.curPos - 5
                elif byte == 0x24: #A1 min
                    A1.desPos =  1
                elif byte == 0x25: #A1 max
                    A1.desPos =  360
                    
                elif byte == 0x30: #Enabled/Disabled
                    A2.enabledCMD = not A2.enabledCMD
                elif byte == 0x31: #Homing Enabled/Disabled
                    A2.homing = not A2.homing
                elif byte == 0x32: #A2 Pos +
                    A2.desPos =  A2.curPos + 5
                elif byte == 0x33: #A2 Pos -
                    A2.desPos =  A2.curPos - 5
                elif byte == 0x34: #A2 min
                    A2.desPos =  1
                elif byte == 0x35: #A2 max
                    A2.desPos =  360
                    
                elif byte == 0x40: #Enabled/Disabled
                    A3.enabledCMD = not A3.enabledCMD
                elif byte == 0x41: #Homing Enabled/Disabled
                    A3.homing = not A3.homing
                elif byte == 0x42: #A3 Pos +
                    A3.desPos =  A3.curPos + 5
                elif byte == 0x43: #A3 Pos -
                    A3.desPos =  A3.curPos - 5
                elif byte == 0x44: #A3 min
                    A3.desPos =  1
                elif byte == 0x45: #A3 max
                    A3.desPos =  360
                    
                elif byte == 0x50: #Enabled/Disabled
                    A4.enabledCMD = not A4.enabledCMD
                elif byte == 0x51: #Homing Enabled/Disabled
                    A4.homing = not A4.homing
                elif byte == 0x52: #A4 Pos +
                    A4.desPos =  A4.curPos + 5
                elif byte == 0x53: #A4 Pos -
                    A4.desPos =  A4.curPos - 5
                elif byte == 0x54: #A4 min
                    A4.desPos =  1
                elif byte == 0x55: #A4 max
                    A4.desPos =  360
                    
                elif byte == 0x60: #Enabled/Disabled
                    A5.enabledCMD = not A5.enabledCMD
                elif byte == 0x61: #Homing Enabled/Disabled
                    A5.homing = not A5.homing
                elif byte == 0x62: #A5 Pos +
                    A5.desPos =  A5.curPos + 5
                elif byte == 0x63: #A5 Pos -
                    A5.desPos =  A5.curPos - 5
                elif byte == 0x64: #A5 min
                    A5.desPos =  1
                elif byte == 0x65: #A5 max
                    A5.desPos =  360
                    
                elif byte == 0x70: #Enabled/Disabled
                    A6.enabledCMD = not A6.enabledCMD
                elif byte == 0x71: #Homing Enabled/Disabled
                    A6.homing = not A6.homing
                elif byte == 0x72: #A6 Pos +
                    A6.desPos =  A6.curPos + 5
                elif byte == 0x73: #A6 Pos -
                    A6.desPos =  A6.curPos - 5
                elif byte == 0x74: #A6 min
                    A6.desPos =  1
                elif byte == 0x75: #A6 max
                    A6.desPos =  360
                    
def setup_nextion_display():
    """Inicializace a nastavení Nextion displeje"""
    # Inicializační příkazy pro displej
    send_to_nextion("page 0")  # Přepnutí na stránku 0
    
    # Reset tlačítek na hodnotu 0
    send_to_nextion("t1.val=0")
    send_to_nextion("t2.val=0")
    send_to_nextion("t3.val=0")
    send_to_nextion("t4.val=0")
    send_to_nextion("t5.val=0")
    send_to_nextion("t6.val=0")
    
    # Nastavení detekce dotyků 
    send_to_nextion("bkcmd=3")  # Plná zpětná vazba

# Inicializace
X_CENTER, Y_CENTER = calibrate_joystick()

# Nastavení Nextion displeje
print("Nastavuji Nextion displej...")
setup_nextion_display()

# Předešlé stavy tlačítek
print("Inicializace dokončena, začínám hlavní smyčku")

def main_thread():
    last_display_update = time.time()
    
    pre_button1 = True
    pre_button2 = True
    pre_button3 = True
    
    # Stavy lokálních tlačítek na Pico, které kopírujeme do Nextion
    local_button0_state = 0
    local_button1_state = 0
    local_button2_state = 0

    nextion_button0_active = False
    nextion_button1_active = False
    nextion_button2_active = False
    nextion_button3_active = False
    nextion_button4_active = False
    nextion_button5_active = False
    nextion_button6_active = False
    nextion_back_button_active = False
    
    while True:
    # Kontrola dat z UART
        check_uart_for_data()
    
    # Čtení joysticku
        x, y = read_joystick()
    
    # Aktualizace hodnot na displeji (méně často)
        current_time = time.time()
        if current_time - last_display_update >= 1:  # Každou sekundu
            last_display_update = current_time
            send_to_nextion(f'txtX.txt="X Position: {x}"')
            send_to_nextion(f'txtY.txt="Y Position: {y}"')
            
            #A1
            send_to_nextion(f'en1.txt="{A1.enabled}"')
            
            send_to_nextion(f'A1Homed.txt="{A1.homed}"')
            
            send_to_nextion(f'm1r.txt="Rotace motoru: {A1.curPos}"')
            
            if (A1.homing):
                send_to_nextion(f'A1HomingCMD.txt="Homing enabled"')
            else:
                send_to_nextion(f'A1HomingCMD.txt="Homing disabled"')


            #A2
            send_to_nextion(f'en2.txt="{A2.enabled}"')
            
            send_to_nextion(f'A2Homed.txt="{A2.homed}"')
            
            send_to_nextion(f'm2r.txt="Rotace motoru: {A2.curPos}"')
            
            if (A2.homing):
                send_to_nextion(f'A2HomingCMD.txt="Homing enabled"')
            else:
                send_to_nextion(f'A2HomingCMD.txt="Homing disabled"')
            #A3
            send_to_nextion(f'en3.txt="{A3.enabled}"')
            send_to_nextion(f'A3Homed.txt="{A3.homed}"')
            send_to_nextion(f'm3r.txt="Rotace motoru: {A3.curPos}"')
            if (A3.homing):
                send_to_nextion(f'A3HomingCMD.txt="Homing enabled"')
            else:
                send_to_nextion(f'A3HomingCMD.txt="Homing disabled"')

            #A4
            send_to_nextion(f'en4.txt="{A4.enabled}"')
            send_to_nextion(f'A4Homed.txt="{A4.homed}"')
            send_to_nextion(f'm4r.txt="Rotace motoru: {A4.curPos}"')
            if (A4.homing):
                send_to_nextion(f'A4HomingCMD.txt="Homing enabled"')
            else:
                send_to_nextion(f'A4HomingCMD.txt="Homing disabled"')

            #A5
            send_to_nextion(f'en5.txt="{A5.enabled}"')
            send_to_nextion(f'A5Homed.txt="{A5.homed}"')
            send_to_nextion(f'm5r.txt="Rotace motoru: {A5.curPos}"')
            if (A5.homing):
                send_to_nextion(f'A5HomingCMD.txt="Homing enabled"')
            else:
                send_to_nextion(f'A5HomingCMD.txt="Homing disabled"')

            #A6
            send_to_nextion(f'en6.txt="{A6.enabled}"')
            send_to_nextion(f'A6Homed.txt="{A6.homed}"')
            send_to_nextion(f'm6r.txt="Rotace motoru: {A6.curPos}"')
            if (A6.homing):
                send_to_nextion(f'A6HomingCMD.txt="Homing enabled"')
            else:
                send_to_nextion(f'A6HomingCMD.txt="Homing disabled"')

    # Čtení aktuálního stavu fyzických tlačítek na Pico
        c_button1 = button1.value()
        c_button2 = button2.value()
        c_button3 = button3.value()
    
    # Zpracování fyzických tlačítek a aktualizace Nextion
        new_button0_state = 0
        new_button1_state = 0
        new_button2_state = 0
    
        if not c_button1 and pre_button1:  # Tlačítko 1 bylo stisknuto
            new_button0_state = 1
    
        if not c_button2 and pre_button2:  # Tlačítko 2 bylo stisknuto
            new_button1_state = 1
    
        if not c_button3 and pre_button3:  # Tlačítko 3 bylo stisknuto
            new_button2_state = 1
        
    # Aktualizace tlačítek na displeji pouze pokud se stav změnil
        if new_button0_state != local_button0_state:
            local_button0_state = new_button0_state
            send_to_nextion(f"r0.val=1")
            send_to_nextion(f"r1.val=0")
            send_to_nextion(f"r2.val=0")
        
        if new_button1_state != local_button1_state:
            local_button1_state = new_button1_state
            send_to_nextion(f"r0.val=0")
            send_to_nextion(f"r1.val=1")
            send_to_nextion(f"r2.val=0")
        
        if new_button2_state != local_button2_state:
            local_button2_state = new_button2_state
            send_to_nextion(f"r0.val=0")
            send_to_nextion(f"r1.val=0")
            send_to_nextion(f"r2.val=1")
    
    # Zpracování tlačítek z Nextion displeje
        if nextion_button0_active:
            print("Zpracování akce pro tlačítko 1 z Nextion displeje")
            nextion_button0_active = False  # Reset příznaku
        
        if nextion_button1_active:
            print("Zpracování akce pro tlačítko 2 z Nextion displeje")
            nextion_button1_active = False  # Reset příznaku
        
        if nextion_button2_active:
            print("Zpracování akce pro tlačítko 3 z Nextion displeje")
            nextion_button2_active = False  # Reset příznaku
        
        if nextion_button3_active:
            print("Zpracování akce pro tlačítko 4 z Nextion displeje")
            nextion_button3_active = False  # Reset příznaku
        
        if nextion_button4_active:
            print("Zpracování akce pro tlačítko 5 z Nextion displeje")
            nextion_button4_active = False  # Reset příznaku
        
        if nextion_button5_active:
            print("Zpracování akce pro tlačítko 6 z Nextion displeje")
            nextion_button5_active = False  # Reset příznaku
        
        if nextion_button6_active:
            print("Zpracování akce pro tlačítko 7 z Nextion displeje")
            nextion_button6_active = False  # Reset příznaku
        
        if nextion_back_button_active:
            print("Zpracování akce pro tlačítko ZPĚT z Nextion displeje")
        # send_to_nextion("page 0")  # například přechod na hlavní stránku
            nextion_back_button_active = False  # Reset příznaku
    
    # Aktualizace předešlých stavů fyzických tlačítek
        pre_button1 = c_button1
        pre_button2 = c_button2
        pre_button3 = c_button3
    
        time.sleep(0.05)
    
def uart_thread():
    uart2 = UART(1, baudrate=115200, tx=Pin(4), rx= Pin(5))
    while True:
        bufR = bytearray(24)
        uart2.readinto(bufR)

        if(len(bufR) == 24): #received something
            if(bufR[0] == bufR[23] != 0): #data valid           
                
                A1.curPos = bufR[1] | bufR[2] << 8
                A1.homed = bufR[3]
                A1.enabled = bufR[19] & 0x1
                
                A2.curPos = bufR[4] | bufR[5] << 8
                A2.homed = bufR[6]
                A2.enabled = (bufR[19] & 0x2) >> 1
                
                A3.curPos = bufR[7] | bufR[8] << 8
                A3.homed = bufR[9]
                A3.enabled = (bufR[19] & 0x4) >> 2
                
                A4.curPos = bufR[10] | bufR[11] << 8
                A4.homed = bufR[12]
                A4.enabled = (bufR[19] & 0x8) >> 3
                
                A5.curPos = bufR[13] | bufR[14] << 8
                A5.homed = bufR[15]
                A5.enabled = (bufR[19] & 0x10) >> 4
                
                A6.curPos = bufR[16] | bufR[17] << 8
                A6.homed = bufR[18]
                A6.enabled = (bufR[19] & 0x20) >> 5
                              
                
                bufS = bytearray(24)
                bufS[0] = bufR[0]


                bufS[1] = A1.desPos & 0xff
                bufS[2] = A1.desPos >> 8
                bufS[3] = A1.homing & 0xff
                
                bufS[4] = A2.desPos & 0xff
                bufS[5] = A2.desPos >> 8
                bufS[6] = A2.homing & 0xff
                
                bufS[7] = A3.desPos & 0xff
                bufS[8] = A3.desPos >> 8
                bufS[9] = A3.homing & 0xff
                
                bufS[10] = A4.desPos & 0xff
                bufS[11] = A4.desPos >> 8
                bufS[12] = A4.homing & 0xff
                
                bufS[13] = A5.desPos & 0xff
                bufS[14] = A5.desPos >> 8
                bufS[15] = A5.homing & 0xff
                
                bufS[16] = A6.desPos & 0xff
                bufS[17] = A6.desPos >> 8
                bufS[18] = A6.homing & 0xff

                bufS[19] = enableListByte()
                
                bufS[23] = bufR[23]
                

                print(bufR)
                uart2.write(bufS)
                
hlavni_vlakno = _thread.start_new_thread(uart_thread, ())
main_thread()

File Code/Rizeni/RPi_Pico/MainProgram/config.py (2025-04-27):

from machine import Pin

#region Motors
class Achse:
    def __init__(self, name, axisNumber, enPin, dirPin, stepPin, homingSensorPin, stepsPerRevolution, maxDegree, microstepping, enabled = 0):
        self.name = name #adding name to identify axes
        self.axisNumber = axisNumber #adding axis number
        self.enPin = Pin(enPin, Pin.OUT) #enable pin
        self.dirPin = Pin(dirPin, Pin.OUT) #direction change pin, high should be clockwise
        self.stepPin = Pin(stepPin, Pin.OUT) #step pin
        self.homingSensorPin = Pin(homingSensorPin, Pin.IN, Pin.PULL_DOWN) #pin with end position sensor, if homed the value is zero
        self.stepsPerRevolution = stepsPerRevolution #steps per revolution
        self.maxDegree = maxDegree #max degree in axis
        self.microstepping = microstepping #microstepping value like full-step or half-step
        self.oneStep = 360/((stepsPerRevolution/microstepping) * 2) #angle change by one step
        self.movingStatus = 0
        self.enabled = enabled

    def __str__(self):
        return f"{self.name},{self.axisNumber},{self.enPin},{self.dirPin},{self.stepPin},{self.homingSensorPin},{self.stepsPerRevolution},{self.maxDegree},{self.microstepping},{self.stepPin}, {self.pos}, {self.desiredPos}" 

    #current positon related things
    def setPos(self, pos):
        self.pos = pos
    
    def getPos(self):
        return self.pos
    
    def stepMade(self, direction): #direction 1 means clockwise
        self.pos = ((self.getPos() + (self.oneStep * direction)) % 360)


    #homing related things
    def setHomedStatus(self, homed):
        self.homed = homed

    def getHomedStatus(self):
        return self.homed
    
    def getHomingSensorValue(self):
        return self.homingSensorPin.value()
    
    
    #desired positon related things
    def setDesiredPos(self, desiredPos):
        self.desiredPos = desiredPos #% 360

    def getDesiredPos(self):
        return self.desiredPos
    
    def setMovingStatus(self, numb):
        self.movingStatus = numb #0 - not started, 1 - moving, 2 - done
        #comm.sendMessage(self.name)
        
    def getMovingStatus(self):
        return self.movingStatus #0 - not started, 1 - moving, 2 - done
    
    

Achsen = []

#A1
Achsen.append(Achse("A1", 1,
                    0, #enPin
                    1, #dirPin
                    2, #stepPin
                    3, #homingSensorPin
                    10745, #stepsPerRevolution
                    90, #maxDegree
                    2, #microstepping
                    1)) #enabled
Achsen[0].setPos(0)
Achsen[0].setDesiredPos(0)
Achsen[0].setHomedStatus(0)
Achsen[0].setMovingStatus(0)

#A2
Achsen.append(Achse("A2", 2,
                    6, #enPin
                    7, #dirPin
                    8, #stepPin
                    9, #homingSensorPin
                    10745, #stepsPerRevolution
                    90, #maxDegree
                    2, #microstepping
                    1)) #enabled


Achsen[1].setPos(0)
Achsen[1].setDesiredPos(0)
Achsen[1].setHomedStatus(0)
Achsen[1].setMovingStatus(0)


#A3
Achsen.append(Achse("A3", 3,
                    10, #enPin
                    11, #dirPin
                    12, #stepPin
                    13, #homingSensorPin
                    10745, #stepsPerRevolution
                    90, #maxDegree
                    2, #microstepping
                    0)) #enabled


Achsen[2].setPos(0)
Achsen[2].setDesiredPos(0)
Achsen[2].setHomedStatus(0)
Achsen[2].setMovingStatus(0)


#A4
Achsen.append(Achse("A4", 4,
                    14, #enPin
                    15, #dirPin
                    16, #stepPin
                    17, #homingSensorPin
                    200, #stepsPerRevolution
                    180, #maxDegree
                    1/4, #microstepping
                    0)) #enabled


Achsen[3].setPos(0)
Achsen[3].setDesiredPos(0)
Achsen[3].setHomedStatus(0)
Achsen[3].setMovingStatus(0)


#A5
Achsen.append(Achse("A5", 5,
                    18, #enPin
                    19, #dirPin
                    20, #stepPin
                    21, #homingSensorPin
                    200, #stepsPerRevolution
                    180, #maxDegree
                    1/4, #microstepping
                    0)) #enabled


Achsen[4].setPos(0)
Achsen[4].setDesiredPos(0)
Achsen[4].setHomedStatus(0)
Achsen[4].setMovingStatus(0)


#A6
Achsen.append(Achse("A6", 6,
                    22, #enPin
                    26, #dirPin
                    27, #stepPin
                    28, #homingSensorPin
                    200, #stepsPerRevolution
                    180, #maxDegree
                    1/4, #microstepping
                    0)) #enabled


Achsen[5].setPos(0)
Achsen[5].setDesiredPos(0)
Achsen[5].setHomedStatus(0)
Achsen[5].setMovingStatus(0)



#endregion

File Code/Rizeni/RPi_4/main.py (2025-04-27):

import serial
import time
from serial.serialutil import SerialException
import random
from threading import Thread

control = serial.Serial("/dev/ttyAMA3", 115200) #UART3, TX=4 RX=5
pendant = serial.Serial("/dev/ttyAMA4", 115200) #UART4, TX=8 RX=9

class Achse:
    def __init__(self):
        self.desPos = 0
        self.curPos = 0
        self.homing = 0
        self.homed = 0

A1 = Achse()
A2 = Achse()
A3 = Achse()
A4 = Achse()
A5 = Achse()
A6 = Achse()

#Allowing homing
A1.homing = 1
A2.homing = 1
A3.homing = 1
A4.homing = 1
A5.homing = 1
A6.homing = 1

#Enabling axis
A1.enabled = 1
A2.enabled = 0
A3.enabled = 0
A4.enabled = 0
A5.enabled = 0
A6.enabled = 0


def enableListByte(): 
    #Value for byte with enabling axis
    enableList = 0
    enableList = enableList | A1.enabled
    enableList = enableList | (A2.enabled << 1)
    enableList = enableList | (A3.enabled << 2)
    enableList = enableList | (A4.enabled << 3)
    enableList = enableList | (A5.enabled << 4)
    enableList = enableList | (A6.enabled << 5)
    return enableList


def randomPos():
    A1.desPos = random.randint(0, 90)
    A2.desPos = random.randint(0, 90)
    A3.desPos = random.randint(0, 90)
    A4.desPos = random.randint(0, 90)
    A5.desPos = random.randint(0, 90)
    A6.desPos = random.randint(0, 90)



#print("Axis 4 is: " + str((enableList & 0x8) >> 3))

#region Control

def comm_Control():

    counter = 1
    lastTime = 0

    print("PySerial version: " + serial.__version__)

    while True:

        control.reset_input_buffer() #reset input before, without this occured many problems
        control.reset_output_buffer()

        #randomPos()
        A1.desPos = 90
        
        #prepare buffer for sending
        bufS = bytearray(24)
            
        bufS[0] = counter
        
        bufS[1] = A1.desPos & 0xff
        bufS[2] = A1.desPos >> 8
        bufS[3] = A1.homing & 0xff
        
        bufS[4] = A2.desPos & 0xff
        bufS[5] = A2.desPos >> 8
        bufS[6] = A2.homing & 0xff
        
        bufS[7] = A3.desPos & 0xff
        bufS[8] = A3.desPos >> 8
        bufS[9] = A3.homing & 0xff
        
        bufS[10] = A4.desPos & 0xff
        bufS[11] = A4.desPos >> 8
        bufS[12] = A4.homing & 0xff
        
        bufS[13] = A5.desPos & 0xff
        bufS[14] = A5.desPos >> 8
        bufS[15] = A5.homing & 0xff
        
        bufS[16] = A6.desPos & 0xff
        bufS[17] = A6.desPos >> 8
        bufS[18] = A6.homing & 0xff
        
        bufS[19] = enableListByte()
        
        bufS[23] = counter
        
        control.write(bufS) #send buffer
        print("Control Data sent!") 
        
        time.sleep(0.2) #wait before receiving
                
        #receiving
        if (control.inWaiting() > 10):
            print("Pico availible!")
            
            bufR = control.read(24)
         
            if(len(bufR) == 24): #received something
                if(bufR[0] == bufR[23] == counter): #data valid
                    counter = counter + 1
                    if(counter >= 256):
                        counter = 1
                    lastTime = time.time() #time when last message was received

                A1.curPos = bufR[1] | bufR[2] << 8
                A1.homed = bufR[3]
                
                A2.curPos = bufR[4] + bufR[5]
                A2.homed = bufR[6]
                
                A3.curPos = bufR[7] + bufR[8]
                A3.homed = bufR[9]
                
                A4.curPos = bufR[10] + bufR[11]
                A4.homed = bufR[12]
                
                A5.curPos = bufR[13] + bufR[14]
                A5.homed = bufR[15]
                
                A6.curPos = bufR[16] + bufR[17]
                A6.homed = bufR[18]
                

                print("Control - Counter1 je: " + str(bufR[0]))
                print("Control - Counter2 je: " + str(bufR[23]))

                #print("{} osa je {}, current pos je: {}, ale desired pos je: {}".format("A1:", str((enableList & 0x1)), str(A1.curPos), str(A1.desPos)))
                #print("{} osa je {}, current pos je: {}, ale desired pos je: {}".format("A2:", str((enableList & 0x2) >> 1), str(A2.curPos), str(A2.desPos)))
                #print("{} osa je {}, current pos je: {}, ale desired pos je: {}".format("A3:", str((enableList & 0x4) >> 2), str(A3.curPos), str(A3.desPos)))
                #print("{} osa je {}, current pos je: {}, ale desired pos je: {}".format("A4:", str((enableList & 0x8) >> 3), str(A4.curPos), str(A4.desPos)))
                #print("{} osa je {}, current pos je: {}, ale desired pos je: {}".format("A5:", str((enableList & 0x10) >> 4), str(A5.curPos), str(A5.desPos)))
                #print("{} osa je {}, current pos je: {}, ale desired pos je: {}".format("A6:", str((enableList & 0x20) >> 5), str(A6.curPos), str(A6.desPos)))


        #print(time.time() - lastTime)
        #print(time.time() - lastTime >= 2.0)
        
        if ((time.time() - lastTime >= 2.0)):
            control.reset_input_buffer() #reset input before, without this occured many problems
            control.reset_output_buffer()
            counter = 1
            print("Control - Connection timed out, current time out time: " + str(time.time() - lastTime))

#endregion

#region Pendant
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

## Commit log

2025-01-22 Bugfixes
    Opravena docela podstatná chyba, teď již v pořádku
    [config.py]
2025-01-22 Rozšíření funkcí
    Příprava pro komunikaci s druhým raspberry, zatím přes tcp, než se mi povede vyřešit převodník napětí pro I2C. Kód ještě potřebuje optimalizaci.
2025-01-23 Nahrání mého progress reportu a opravení názvu složky
    [Deska Top.stl, Deska dole.stl, Podložka pro M2.stl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]
2025-01-24 Progress Report Leden
2025-03-02 Progress report
    [ControlHead.kicad_pcb, ControlHead.kicad_sch]
2025-03-18 ControlHead -> ControlCabinet
    Přejmenování + skoro finální verze
    [ControlCabinet.kicad_pcb, ControlHead.kicad_pcb, ControlHead.kicad_sch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]
2025-03-18 Nové verze kódů pro obě Raspberry
2025-03-20 Postup za Únor
    [schema.kicad_pcb, schema.kicad_sch]
2025-04-01 Progress report Brezen + zavisle soubory
    [Cabinet - back.idw, Cabinet - back.ipt, Cabinet - bottom.idw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]
2025-04-20 PR_Březen
    [schema-B_Cu.gbr, schema-B_Mask.gbr, schema-B_Paste.gbr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]
2025-04-30 Gitlab dokumentace
    [JST_EH_S4B-EH_1x04_P2.50mm_Horizontal.ipt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]
